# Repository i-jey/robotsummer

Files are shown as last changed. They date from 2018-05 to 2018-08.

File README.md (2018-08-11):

ENPH Second Year Summer 
=====

## Description 
Repo to host team code, docs, CAD models, circuit schematics and other useful items. 

## COMPETITION RUNS 
[Video of all teams at competition here.](https://www.youtube.com/watch?v=OxAf1p7clqE)

Our runs found at: 

* [8:40](https://youtu.be/OxAf1p7clqE?t=8m40s)

* [46:23](https://youtu.be/OxAf1p7clqE?t=46m23s)

* [1:07:25](https://youtu.be/OxAf1p7clqE?t=1h7m25s)

* [Tape follower: 57:10](https://youtu.be/OxAf1p7clqE?t=57m10s)

## Documentation site 
https://i-jey.github.io/robotsummer/

## Calculation Spreadsheet
https://docs.google.com/spreadsheets/d/1G_nlOqhw7OiXAsn64Kg7ZWVn5ETo55PLTQZf5VaNq4Y/edit#gid=240156634

## First Design Review 
https://docs.google.com/presentation/d/1Tin1bqWngJIaByWks2kfljkIxHQzdjXB50zxXt77TIM/edit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

STM32
===

## Key pins
---
|Key Pins 	|Description 	|Notes 	|
|:-:	|:-:	|:-:	|
|A9 	|TX1 	|Connect to RX on the Serial port connector 	|
|A10 	|RX1 	|Connect to TX on the Serial port connector 	|
|B6 	|SCL1 	|OLED display 	|
|B7 	|SDA1 	|OLED display 	|

## Uploading code 
---
If the code fails to upload, the error is usually one of the following: 
1. The platformio.ini is missing the `upload_protocol = serial` and `upload_port = COMX` settings.
2. RX / TX pins have been mixed up from the STM to the serial port connector. They should go to the opposite pins on the serial port connector. 
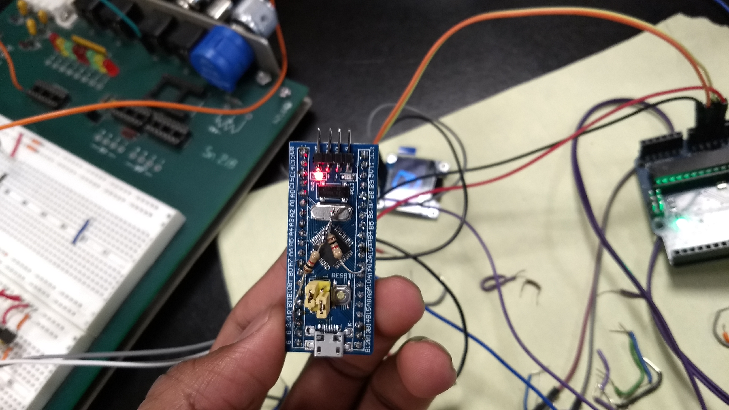
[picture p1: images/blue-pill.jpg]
3. The jumper is not in the correct position. 

## Pinout Reference
---
Pinout

Electrical Circuits
===

## High-side driver H-Bridge
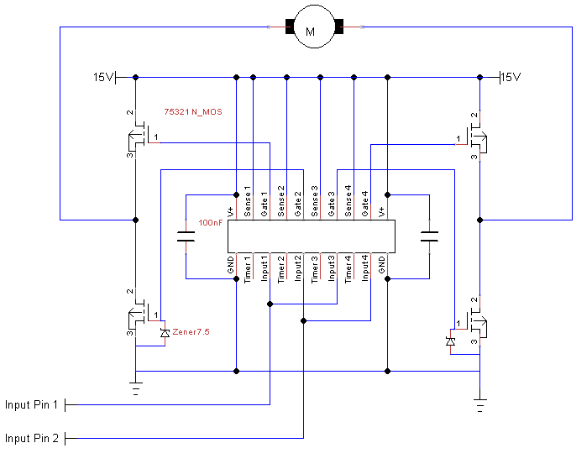
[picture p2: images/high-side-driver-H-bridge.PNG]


Wiring Check
===
1. Left Panel
2. Right Panel
3. Main Ground
4. 16V Rail
5. Control Panel Signal
6. Conntrol Panel Power
7. Potentiometer 
(FINISHED EDITING)

Tricks
===
1. Capacitors between power and ground prevent the bluepill from turning off when the H-bridges turn on. A 470uF capacitor keeps the bluepill powered at 3.3V for long enough when the voltage of the rest of the battery drops due to the sudden current draw of the h-bridges.

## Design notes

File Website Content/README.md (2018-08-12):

Documentation Materials 
=== 

Place your content in the relevant folders (images, text+explanations, diagrams). Also add any photos you have of the robot or just general lab stuff into their respective folders too.

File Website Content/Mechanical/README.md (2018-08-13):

Mechanical Components, STLs, design decisions etc.
=== 

## Chassis

PL2 W7K's chassis was constructed primarily out of lasercut hardboard. The chassis was designed in a modular fashion, separating the robot into sections containing the main functional zone, the electrical compartment, and an external drivetrain mounted underneath

## Drivetrain

PL2 W7K consisted of an external/removable drivetrain subassembly, consisting of two independent barbercoleman DC motors and a 1:3 motor-to-wheel gear ratio to provide a strong balance between torque and speed

## Claws

Mirrored side claws were implemented to enable rapid deployment and simple functionality. Constructed from waterjet sheetmetal, the outstretched arms allowed PL2 to grab and rescue ewoks without ever stopping

## Bridge deployment

Gaps in the course were tackled with a forklift-style bridge deployment mechanism. Front arms were lasercut from acrylic plastic to allow fast and controlled bridge laying

## Basket mechanism

A removable basket was also lasercut from hardboard. A metal hook was added with bearings to ensure the basket could easily slide down the zipline on the course. The basket was deployed using a platform and pulley system, powered by a continuous servo

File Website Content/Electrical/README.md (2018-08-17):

Electrical Components, Debugging, Diagrams etc.
=== 

## Motor Drivers

PL2 used H-bridges to allow motors to be driven at high voltages and currents while being controlled through low-voltage signals from the Bluepill mirco-controller. Our h-bridges consist of electrical switches (N-Type MOSFETS) controlled by a high-side gate driver IC chip which recieved PWM outputs from the Bluepill. Each H-bridge was decoupled through capacitors along input and output voltage lines so that noise propagation would not influence other componants in the electrical system.

## IR detection circuits

One of the obstacles of the course was decoding an infra-red signal beacon. This beacon was placed just before the archway, and it's signal would switch randomly between flashing at a frequency of 1kHz and 10kHz. If the robot passed throught the archway when the signal was at 1kHz a platform beyond the archway would start rotating, breaking the tape the robot used to navigate the course. PL2 had two IR detection circuits were used to differentiate the beacons 1kHz and 10kHz respectivly. Both circuits where identical, with the exception of the filter explained below.

This analog circuit was a series of signal manipulators to decode the flashing of the beacon into a signal understood by the Bluepill mirco-controller. The componants of the circuit are as followed:

1. DC-Block

      The DC-Block was used to eliminated the steady 60Hz infra-red emitted from the standard household lights as a part of the competition enviroment.
      
2. Amplify

      At a distance that was relevant to robot manuverability the signal would come across quite weak (in the milli-volts range) the amplificating was used to strengthen the incoming signal.
      
3. Active Filtering

      Since PL2 was required to differentiate 1kHz and 10kHz, the respective circuits were built using Op-Amps (Operational Amplifiers) and RC circuits to ignore the opposite frequency.

4. Analog to Digital Conversion and Amplification

      The final conversion is required to turn the detection of the appropriate signal into a digital high that the mirco-controller may interpret. An extra amplification circuit was required in the event that the non-fluctuating voltage is not large enough for the mirco-controller to read a digital high.
      
### Inverter

As a part of the analog circuits, a switching-inverter was used to supply -VCC to the operational amplifiers.

## Attempted: Encoders

Orginially it was planned to include encoders in the development of PL2 to aid in the navigation of the course. In retrospect we should have started the development of the Encoder interpretation much sooner to ensure reliable usage. The primary difficulty was recieving a steady, noise-free pulse signal from the encoders. As an encoder rotates two switches are turned on and off. The mirco-controller may interpret distance through the number of times the switches are turned on, and direction through the high/low phase shift between the two switches. Due to mechanical inaccuracies the signal was very noisy and, initially, the mirco-controller would read high when it should not have, thus, misinterpreting the signal. 

To fix this we built a RC filter circuit and Schmitt-trigger to filter out high frequency noise, and to employ hysteresis to ensure a clean pulse signal could be read by the mirco-controller. As mentioned before, this development occured too late, for we had already started to used hardcoded motor-on times for precise movements. 

## Attempted: IR Signal Direct Read

Due to the extremely fast clock cycle of the Bluepill mirco-controller (72MHz) it is very possible to directly interpret signals at a frequency in the kHz range as required for the competition. The circuit was simply an amplifier and comparator to ensure the signal was properly read, and the sine wave was converted into a pulse. This development also occurred too late in the 6 week timeline and while it did work, it was a back-up plan in the event the analog circuits failed for some unknown reason.

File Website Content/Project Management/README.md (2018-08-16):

PM Stuff, Team Collaboration etc. 
=== 

## Titles
Team #0

Robot: PL2 W7K (Pronounced "Please Work")

## The Challenge: Ewok Rescue
The 2018 ENPH253 challenge revolved around rescuing 4 plush ewoks and Chewbacca from the imperial fortress. Obstacles included two gaps/valleys in the course, an infrared-triggered spinning platform, two (optional) ziplines, and a pathless bridge separating Chewbacca from the rest of the course.

*The full rules of the competition can be found [here](https://docs.google.com/document/d/18rYIVlMZeD559deR7-5YjfQzZz4BeeS6pr8FI5Qlm8Q/edit)*

## The Strategy: Strategy and PL2 W7K
Our approach to completing the course was to have a separate mechanism for each obstacle. We designed a forklift-style mechanism to lay a bridge over the gaps. The infrared-triggered spinning platform was avoided using an active-filtering IR detection circuit. The bridge mechanism allowed us to avoid requiring the first zipline, while the second was used to transport our ewok-filled basket back to the "safe zone". The pathless bridge would be traversed using edge detection-and-follow algorithm.

PL2 was designed to be **compact**, **fast**, and **nimble**. Ewok-grabbing claws were implented in a way that allowed the robot to grab the ewoks without ever having to stop moving. Ultimatly, this was critical in our success. Since our robot could complete the course so quickly in the alotted 2 minutes we could run twice, the only robot to do so, negating any preformace deficiencies due to random unpredicable errors

## The Result: How we did
PL2 was able to consistently rescue 3 of the 5 plushies, obtaining a total of 9 points (out of 17 - Chewbacca was worth extra). Due to time constraints, we were not able to implement the second half of the course, meaning that we did not get to Chewbacca. Rather, we focused on speed and consistency, bearing us 5th place of 16 in the final competition.

## The Takeaway: What we learned
The team picked up many "dos and don'ts" along the way, as we strongly noticed what worked and what did not work. Perhaps our biggest takeaway was to plan "the small things" thoroughly to avoid spending time on them later. Examples:

- Avoid using header pins - they do not make reliable connections in wired applications

- Just commit to wire placement - Many times we were using connections that would disconnect consitantly, creating a very unreliable system. Having never designed wire managment before we were worried about changing are minds with how we did something, thus having to restart. We ended up changing how we managed our wired three times (complete reboot with solder) anyway and it would have saved time if we just commited and tried sooner.

- Decoupling Capacitors - Saved our lives. At one point when the 14.5V rail was activated and our motors started the Bluepill mirco-contoller would reset. This was likely caused through an extremly fast voltage drop along the 3.3V rail powering the mirco-contoller. A 500uF capacitor fixed that up instantly through maitining the 3.3V rail high enough for the brief moment it dropped.

- Design modularly - ensure that each part/system can be easily accessed, replaced and maintained without interfering with other systems. We learned this specifically with our powertrain. It was detachable, thus, changes could be made without invading on the rest of the chassis design.

- Continuously test - test subsystems, systems and sequences not only for functionality but also for consistency alongside development to save time debugging

- Sample size - consider outliers in your analysis but do not base your judgement single occurrences (for both failures and successes)

- Task Delegation - At some points, mainly during testing, it was not necessary for every group memeber to be present. In the event of too many people working on one componant the multitude of opinions bogged down progress. This being said, it was critical in many situations that more than one person was reviewing work to ensure mistakes where not being missed for a long time.

- Late Nights - Sometimes staying up to un-Godly hours was more of a way to have fun the work efficiently..

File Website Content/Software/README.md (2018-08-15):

Code structure, decisions, weird STM32 stuff etc.
=== 

The brain of PL2 W7K was the STM32 "Blue Pill" microcontroller. The small size, fast clock speeds, and large pinout arrays made the blue pill the top choice for a compact robot. A C++ framework enabled object-oriented Arduino-style code, allowing for modular and easily-integratable components and sequences.

## Menu/control system

A multi-menu control panel was implemented on to the side of PL2 to allow for on-the-spot value adjustment and testing.

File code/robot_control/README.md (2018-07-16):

Control Code 
=== 

VSCode and PlatformIO
--- 
1. [Download VSCode](https://code.visualstudio.com/download)
2. [Install PlatformIO](https://platformio.org/get-started/ide?install=vscode)

src/
--- 
This is where the main jazz is located. Things have been modularized so far by sequences (i.e bridge deployment sequences, claw sequence, basket sequence). You'll find `.h` and `.cpp` files here (abstracts and implementation respectively). 

All those files may have you feelin' a ways, but have no fear. The header files, `.h` are just templates that declare what functions/variables are in use for a given file (class). Reading through the header files is probably a good way to get an idea of how the code is laid out (i.e the function abstracts). `includes.h` bundles everything together so that we can reference them from the main control loop.

`main.cpp` is where the control loop runs, and where constants are set. The different sequences are called in the loop and the actual reading of sensors/writing to motors occurs within the implementation of each sequence (e.g look at `clawSequence.cpp` and `claw.cpp`). 

I need to hit up Amar to find out if it's better practice to set constants in a separate header file or what, but for now it's a minor point. 

Module overview and associated constants
--- 
* Motor 
    1. P, I, D constants
    2. PID speed
    3. PID QRD Threshold
    4. 
* Claw 
    1. a
* Bridge 
    1. b
* Basket
    1. c
* Infrared sensor
    1. d

TODO
---
`July 15th, 2018`
1. Finish adding menu options (dynamically add case values as opposed to hardcoding) 
2. Implement EEPROM to store menu values

OLD
1. <del> [Penned for later, or never lol]Create (i.e update) the current `control flow diagram`. Understand states of different sequences, when they have to override/interact with one another (e.g when ir detected we need to change claw control state, or when second bridge deploys we need to change motor control state)
2. <del>Add in a `flag` in `bridge.cpp/bridge.h` so we know when to `switch from tape following to edge detection`. After the second edge is detected we need to do some custom movement.
    - Rotate 90 left, drop bridge, move a set distance w/ wheel encoders, rotate 90 left, drive forward w/ edge detection.
3. <del>Write `Gate (IR) sequence` (i.e set flag to keep left claw raised, raise both claws going through gate). **Note**: This means `clawSequence` will probably need to be updated to chillax while the gateSequence is going on. 
4. <del>Need to think about how motor control is going to get passed around, i.e from tape control to edge detection to bridge deployment to resuming. And the again, when second edge is detected, rotation, bride deployed, edge detection initiated. (control flow diagram will help with this)
5. <del>Figure out how to set up the `menu system` (how to navigate, how to set variables) using the OLED and then start up the contorl loop. Lower priority for now, setting up base of architecture first. 
6. <del>[Changing to uint8_t breaks stuff, can figure this out later]Convert types to standard definition (i.e 8-bit unsigned integer -> uint8_t)

Lastly, thank you for reading. 

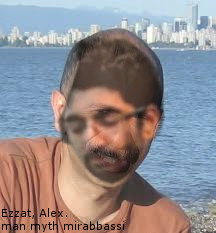
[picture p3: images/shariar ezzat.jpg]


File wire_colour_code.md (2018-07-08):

<span style="color:black">Black-Ground</span>
<br>
<span style="color:red">Red-High Voltage (15V)</span>
<br>
<span style="color:orange">Orange-Mid Voltage (5V)</span>
<br>
<span style="color:yellow">Yellow-Low Voltage (3.3V)</span>
<br>
<span style="color:purple">Purple-Intermediary Wires (High Voltage)</span>
<br>
<span style="color:blue">Blue-Intermediary Wires (Low Voltage)</span>
<br>
<span style="color:green">Green-Servo Signal</span>
<br>
<span style="color:white">White-Motor Signal</span>
<br>
<span style="color:grey">Grey-QRD Signal</span>
<br>
<span style="color:grey">Grey-IR Signal</span>

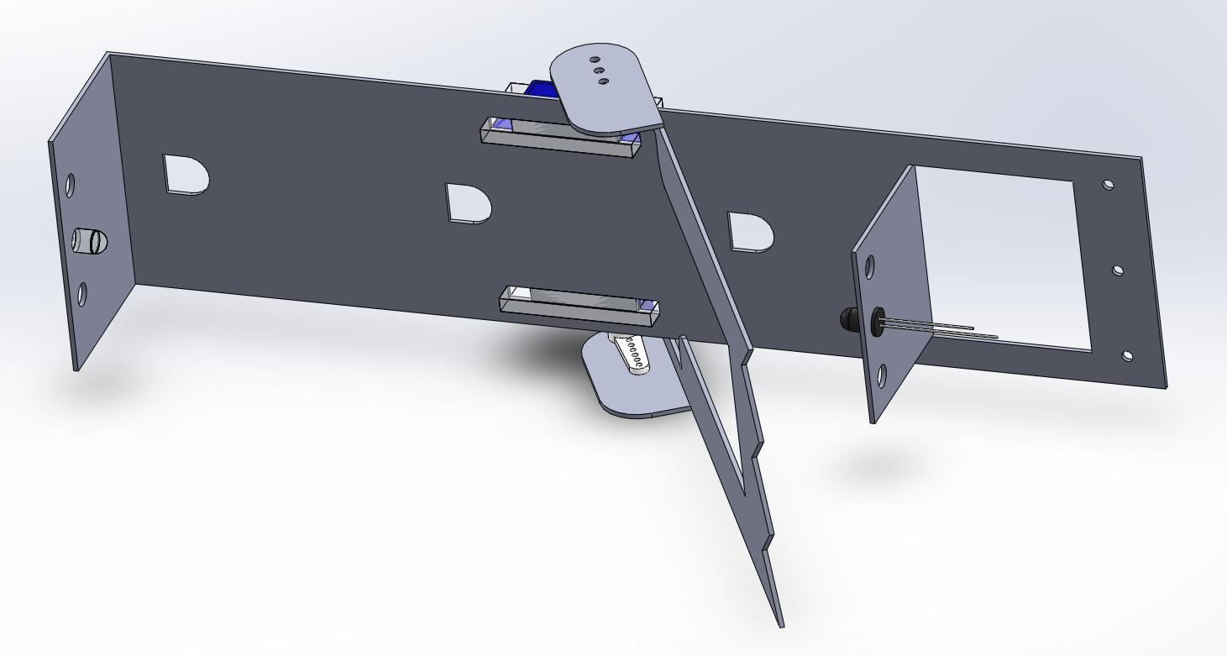
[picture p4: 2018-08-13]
Website Content/Mechanical/CADScreenshots/IsolatedArmView.PNG

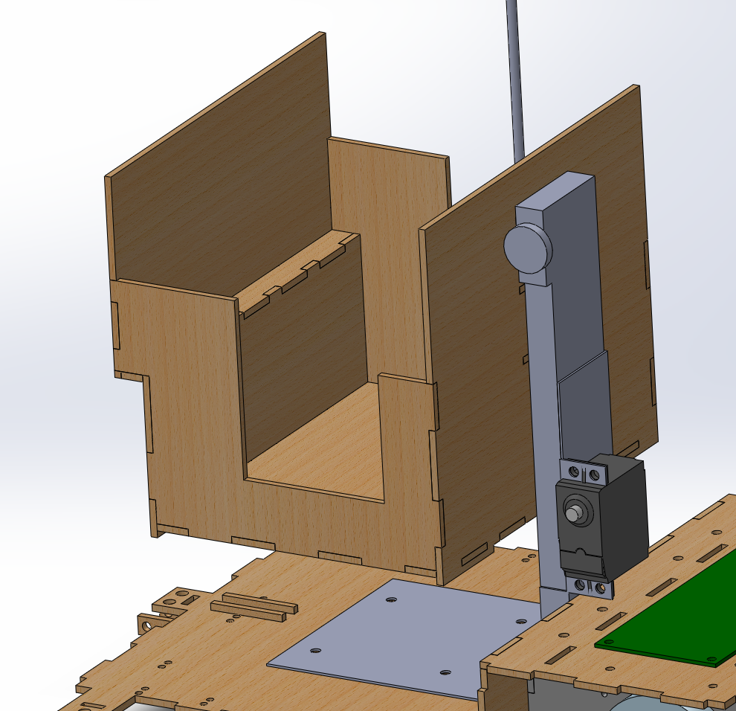
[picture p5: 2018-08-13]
Website Content/Mechanical/CADScreenshots/BasketRaisingMechanism.PNG

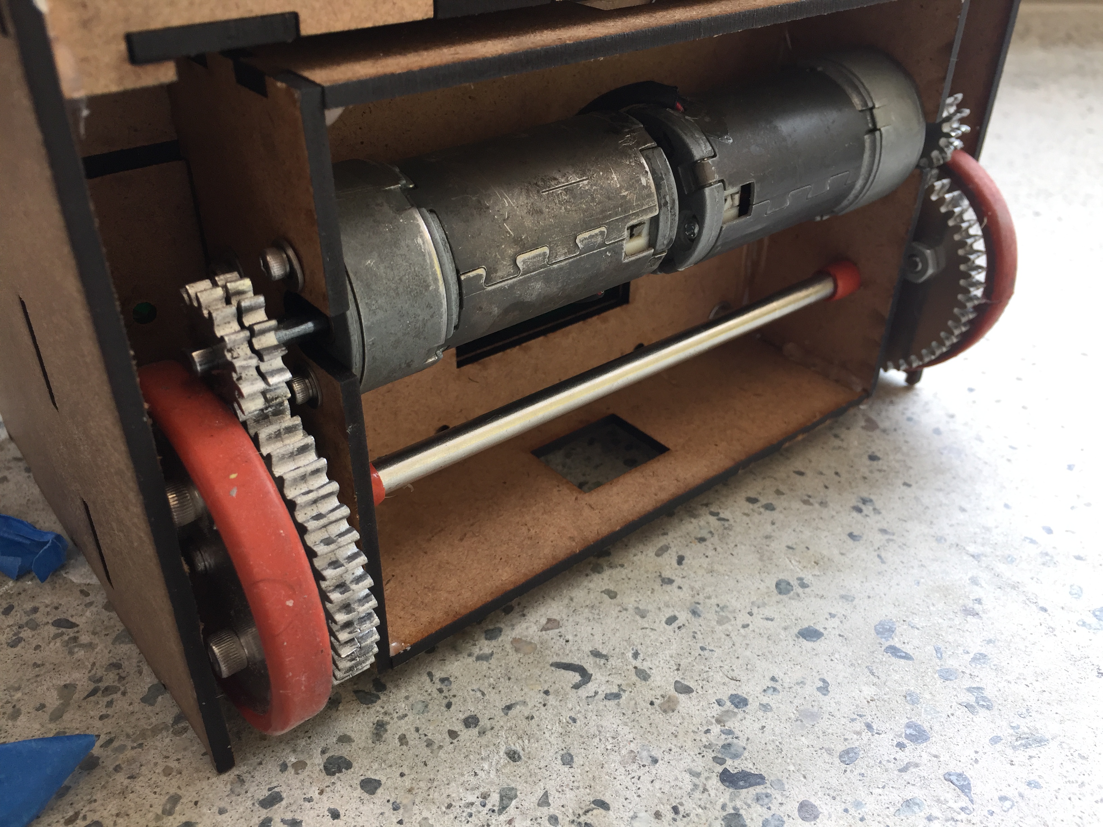
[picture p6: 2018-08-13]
Website Content/Mechanical/Drivetrain2.JPG

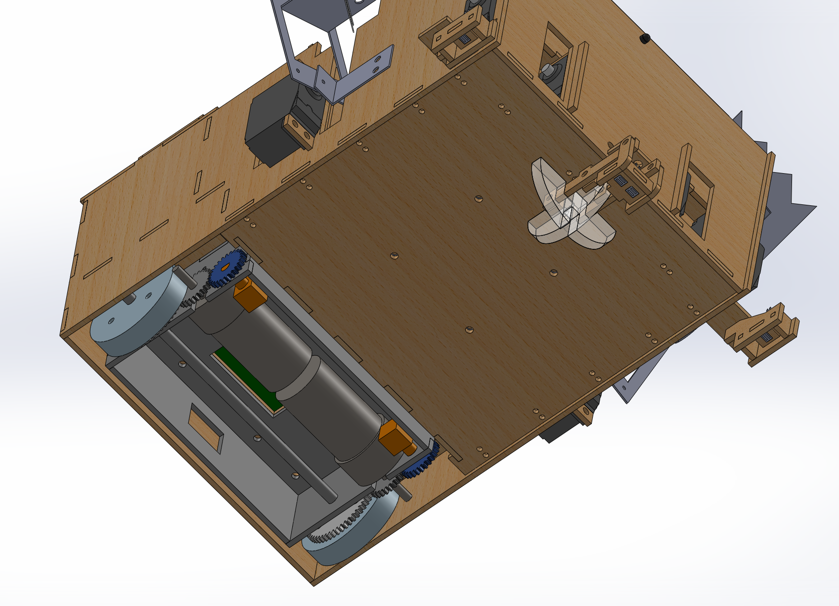
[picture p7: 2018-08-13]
Website Content/Mechanical/CADScreenshots/Drivetrain&BottomView.PNG

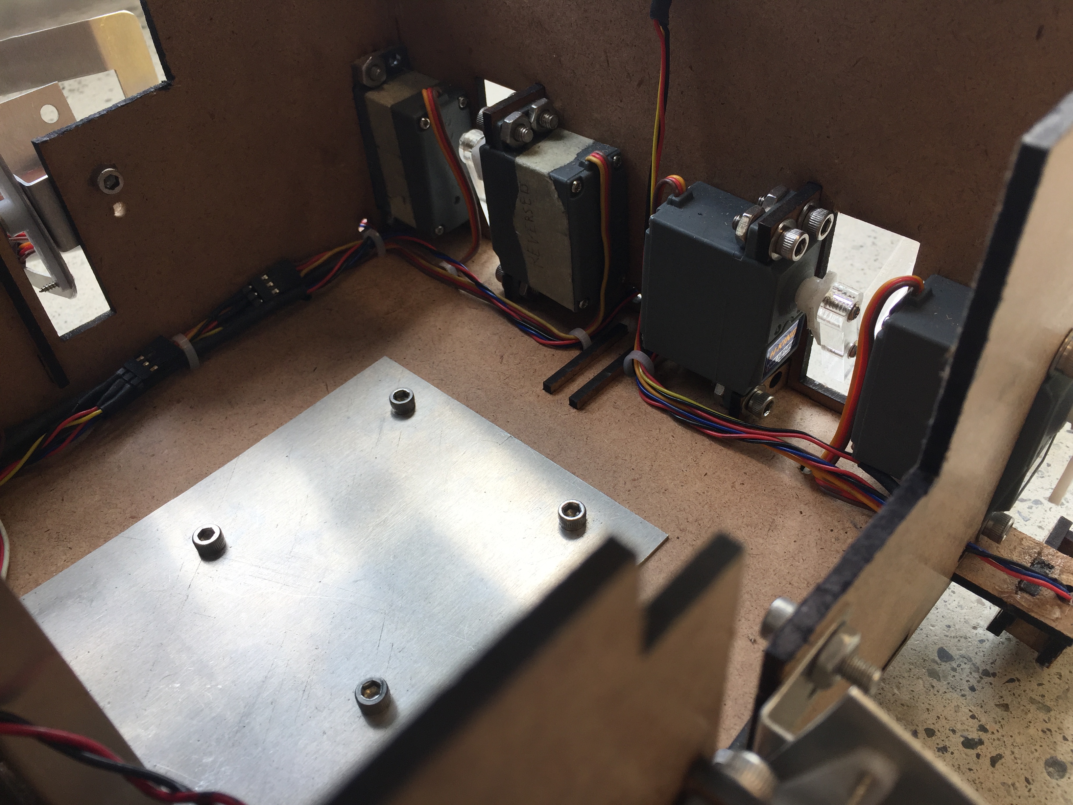
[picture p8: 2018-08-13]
Website Content/photos_of_robot/InsideChassis3.JPG

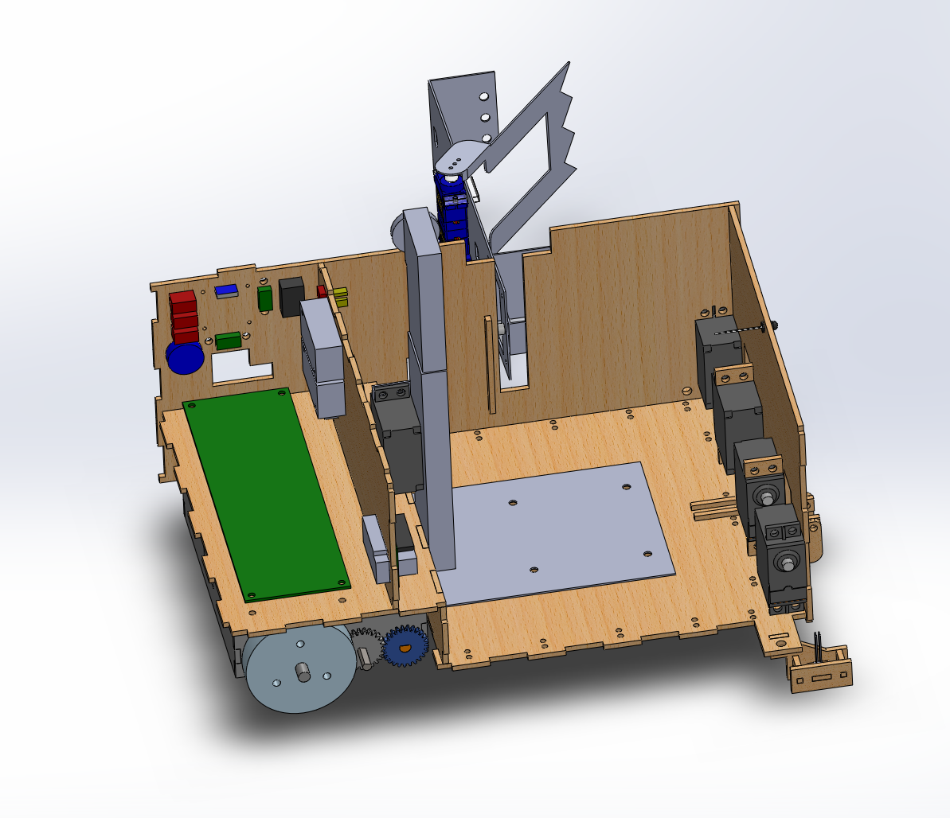
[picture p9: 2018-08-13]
Website Content/Mechanical/CADScreenshots/OpenView.PNG

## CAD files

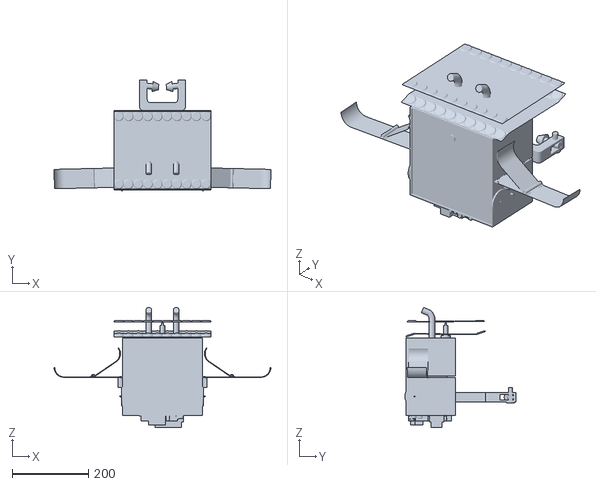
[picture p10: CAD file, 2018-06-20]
cad_models/LukeSkyWaltham.STL
568.9 x 292.2 x 315.1

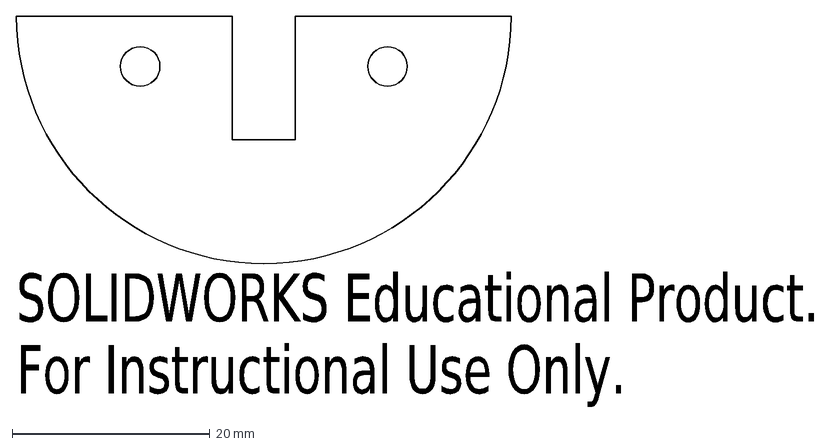
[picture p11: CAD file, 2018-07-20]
cad_models/V3/Acrylic parts/SliderPc1.DXF
SOLIDWORKS Educational Product.
For Instructional Use Only.

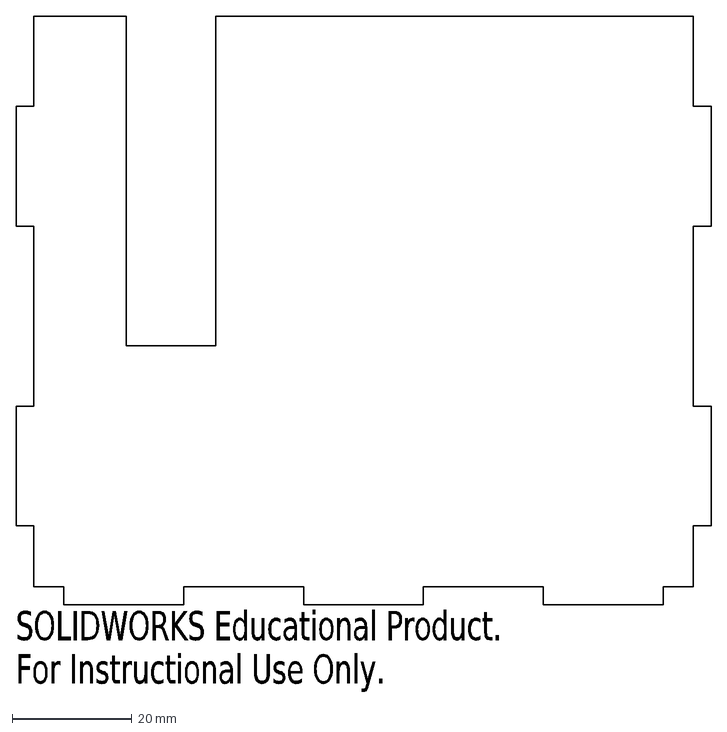
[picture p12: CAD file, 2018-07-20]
cad_models/V3/Basket/BasketV3SidePanelx2.DXF
SOLIDWORKS Educational Product.
For Instructional Use Only.

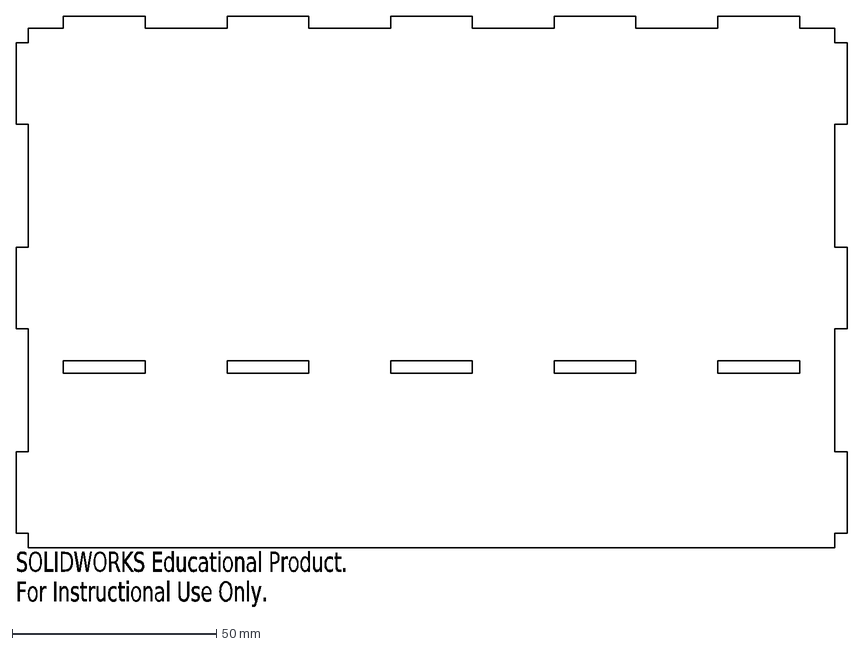
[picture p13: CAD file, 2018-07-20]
cad_models/V3/Chassis/ChassisV3BackPanel.DXF
SOLIDWORKS Educational Product.
For Instructional Use Only.

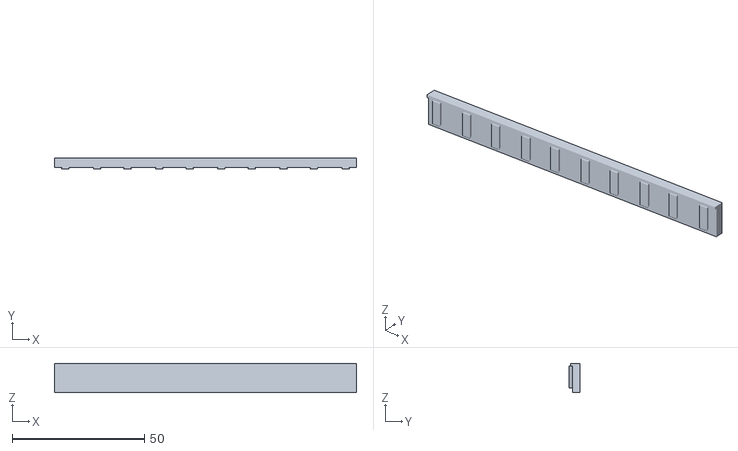
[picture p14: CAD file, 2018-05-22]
docs/AlexEzzat_54_MaleSide.STL
114.2 x 4.30 x 11.0

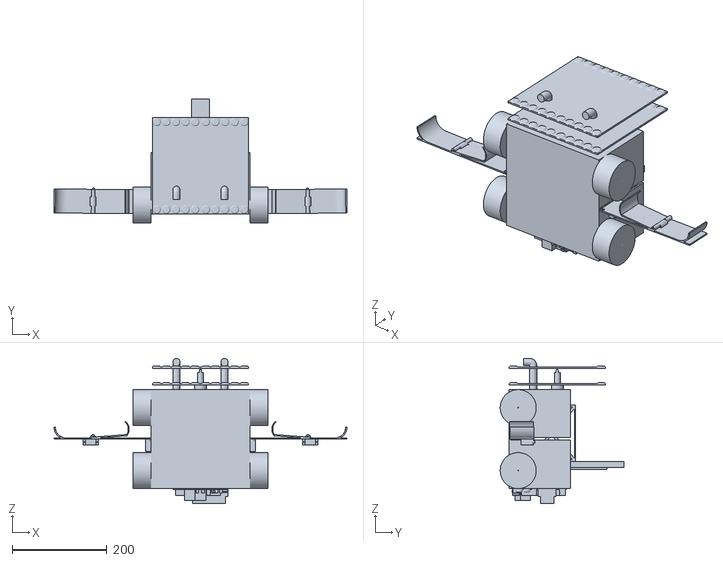
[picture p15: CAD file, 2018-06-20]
cad_models/DoubleBridger.STL
619.4 x 261.3 x 306.9

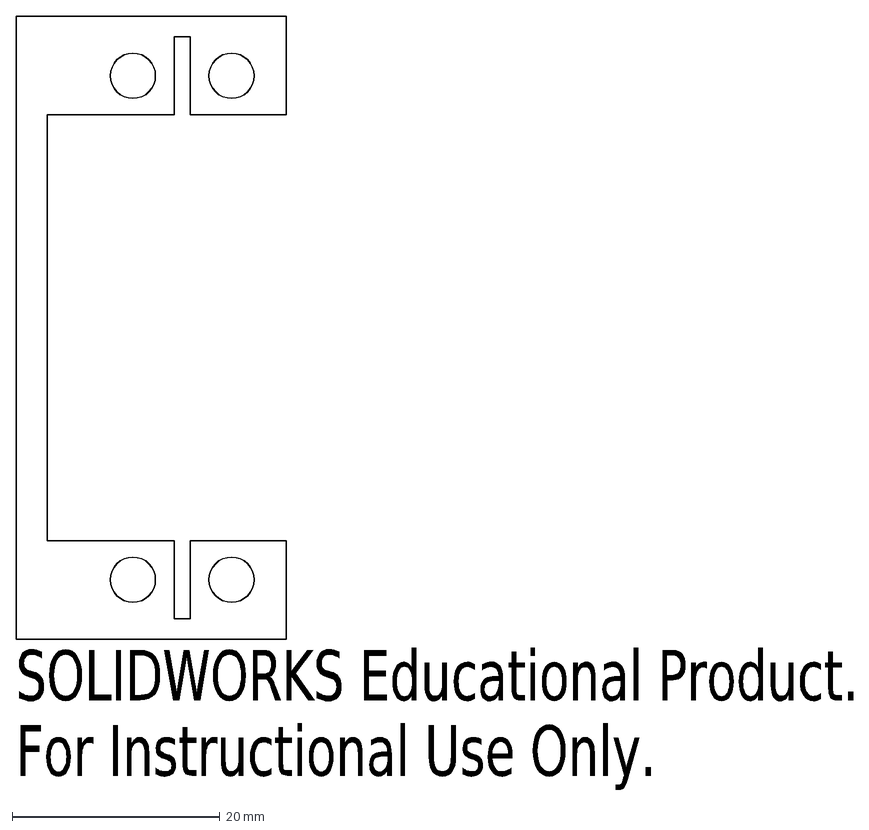
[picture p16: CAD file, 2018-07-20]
cad_models/V3/Acrylic parts/LargeServoHolderx4.DXF
SOLIDWORKS Educational Product.
For Instructional Use Only.

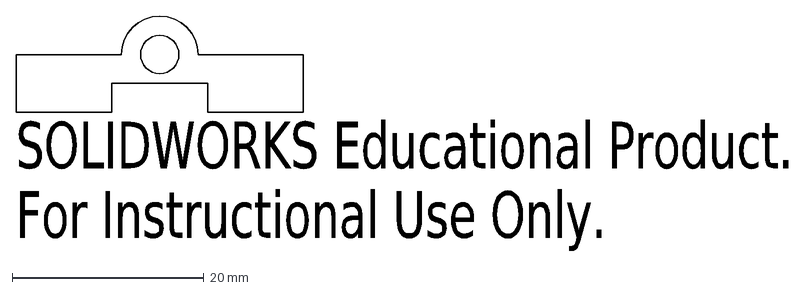
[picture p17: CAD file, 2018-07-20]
cad_models/V3/Basket/BasketRodHolderx3.DXF
SOLIDWORKS Educational Product.
For Instructional Use Only.

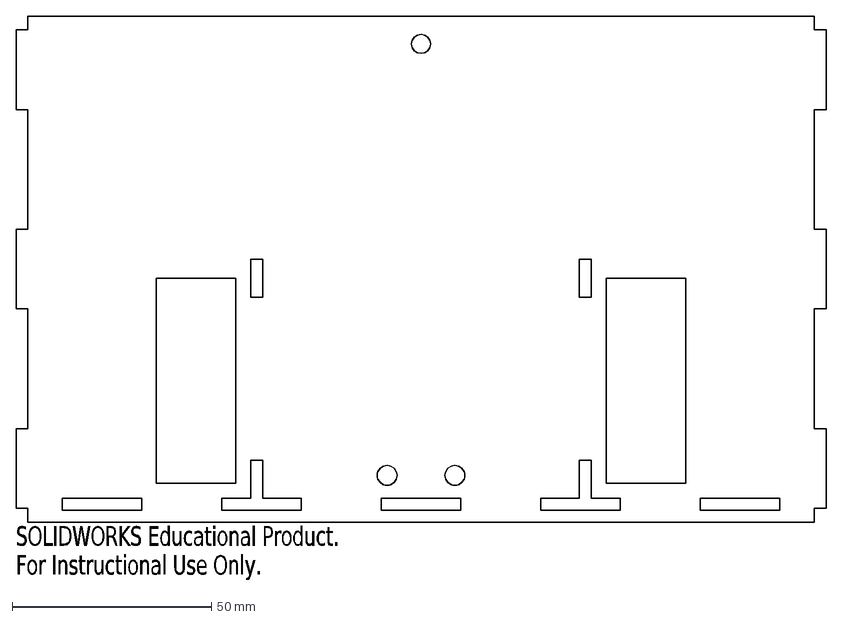
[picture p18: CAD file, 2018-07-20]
cad_models/V3/Chassis/ChassisV3FrontPanel.DXF
SOLIDWORKS Educational Product.
For Instructional Use Only.

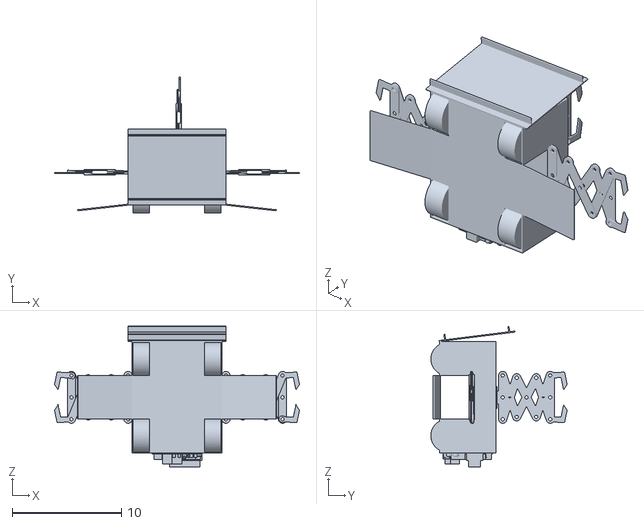
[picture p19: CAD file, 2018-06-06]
cad_models/FlatBot.STL
22.4 x 12.5 x 12.8

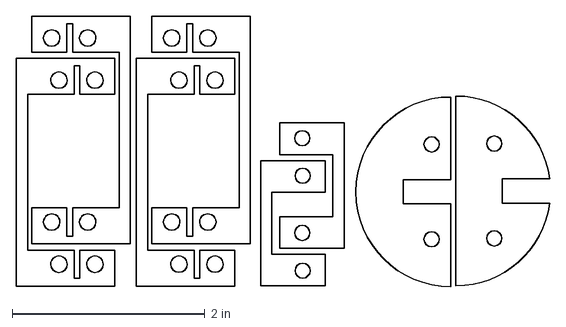
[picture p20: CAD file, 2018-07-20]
cad_models/V3/Acrylic parts/Acrylic DXF.dxf
5.54 x 2.81 in

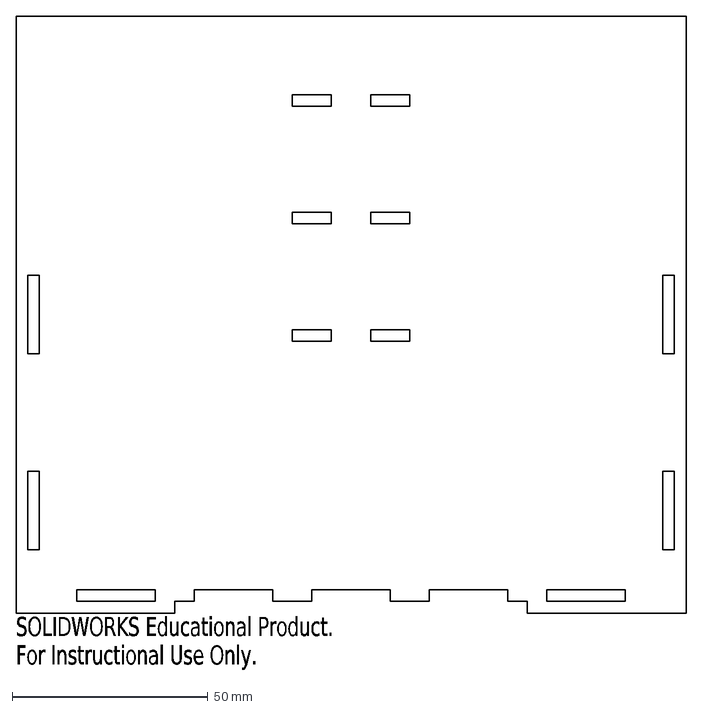
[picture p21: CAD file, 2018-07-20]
cad_models/V3/Basket/BasketV3BackPanel.DXF
SOLIDWORKS Educational Product.
For Instructional Use Only.

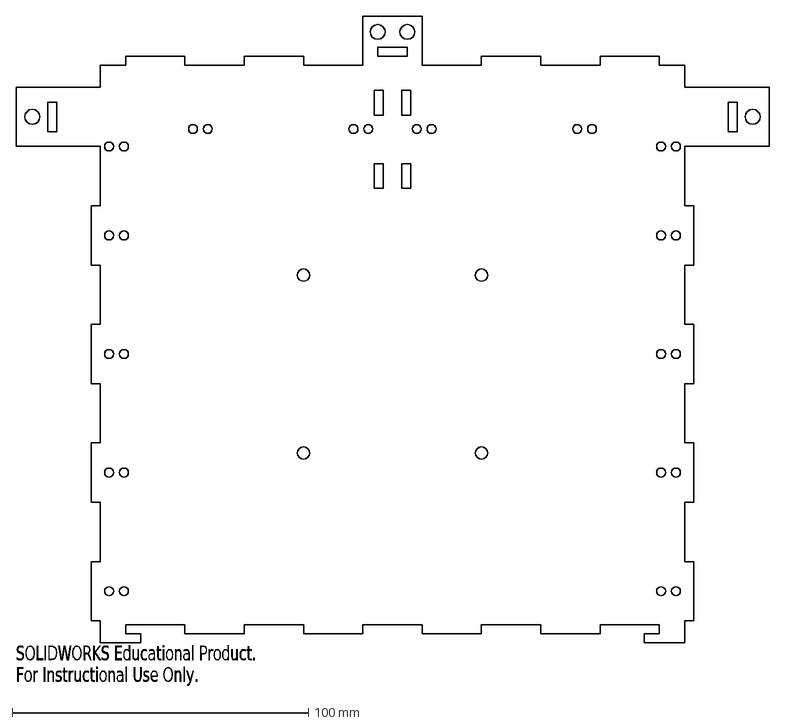
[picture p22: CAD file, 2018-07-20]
cad_models/V3/Chassis/ChassisV3LowerBottomPanel.DXF
SOLIDWORKS Educational Product.
For Instructional Use Only.

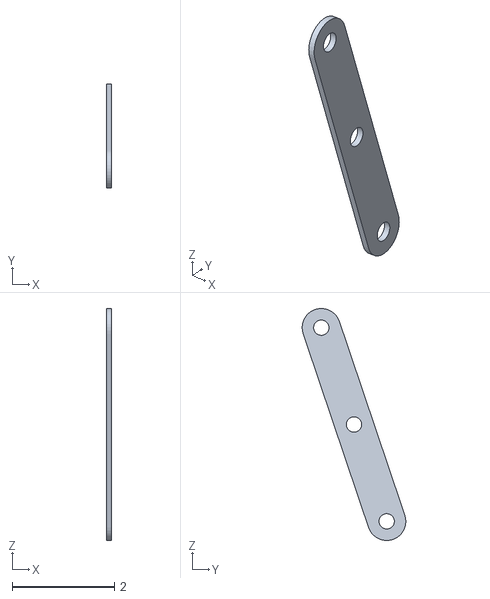
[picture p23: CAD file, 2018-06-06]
cad_models/FlatBot - Claw Arm-3 Claw Arm BracketComponent-2.STL
0.1 x 2.03 x 4.54

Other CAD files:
cad_models/V3/Acrylic parts/SliderPc2.DXF
cad_models/V3/Basket/BasketV3FrontPanel.DXF
cad_models/V3/Chassis/BatteryHolderSidePanelx2.DXF
cad_models/FlatBot - TINAH board-1.STL
cad_models/FlatBot - 3in Wheel-1.STL
cad_models/FlatBot - 3in Wheel-2.STL
cad_models/FlatBot - 3in Wheel-3.STL
cad_models/FlatBot - 3in Wheel-4.STL
cad_models/FlatBot - Bridge-1.STL
cad_models/FlatBot - Chassis Lid-1.STL
cad_models/FlatBot - Chassis Ramp-1.STL
cad_models/FlatBot - Chassis Ramp-2.STL
cad_models/FlatBot - Claw Arm-1 Claw Arm BracketComponent-1.STL
cad_models/FlatBot - Claw Arm-1 Claw Arm BracketComponent-2.STL
cad_models/FlatBot - Claw Arm-1 Claw Arm BracketComponent-3.STL
cad_models/FlatBot - Claw Arm-1 Claw Arm BracketComponent-4.STL
cad_models/FlatBot - Claw Arm-1 Claw Arm BracketComponent-5.STL
cad_models/FlatBot - Claw Arm-1 Claw Arm BracketComponent-6.STL
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

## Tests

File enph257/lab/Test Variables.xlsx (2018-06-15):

 | Variables
Test Number | c | k | Pin | kc | e
1 | 921 | 300 | 10 | 12.5 | 0.2
2 | 921 | 500 | 11 | 12.5 | 0.2
3 | 1400 | 200 | 11 | 15 | 0.4
Changed Starting Tempurature
4 | 1200 | 200 | 8.5 | 9.25 | 0.4
5 | 1400 | 200 | 8.5 | 9.25 | 0.4
6 | 1200 | 175 | 12.5 | 9.5 | 0.2
7 | 1300 | 175 | 10 | 8 | 0.25
7 | 1100 | 250 | 10 | 8 | 0.25
9 | 1100 | 150 | 11 | 8 | 0.2
10 | 921 | 220 | 11.5 | 8.2 | 0.2

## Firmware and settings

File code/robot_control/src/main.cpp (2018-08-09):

#include "includes.h"
#pragma GCC diagnostic ignored "-Wwrite-strings"

constexpr int INSIDE = 1; 

// Global variable initialization 
int globalMotorStateTracker = 0; 
int prevEwokCounter = 0; 
int ewokCounter = 0; 
int rightClawState = 0; 
int leftClawState = 0; 

// EEPROM / menu reference 
enum MenuItems {
    menu_qrdThreshold,
    menu_p,
    menu_d, 
    menu_gain,  
    menu_defaultSpeed, 
    edgeThresh, 
    firstBridgeLowerAngle, 
    firstBridgeUpperAngle, 
    edgeReverseDistance, 
    dropBridgeDistance, 
    driveOverDistance, 
    s3Tilt, 
    s3Reverse, 
    s3Drop, 
    s3Pullback, 
    pidTime, 
};

// Menu pins 
constexpr int startBtn = PC15;
constexpr int menuMinus = PA12; 
constexpr int menuToggle = PA15; 
constexpr int menuPlus = PA11; 
constexpr int menuPot = PB1; 

// Oled pins 
constexpr int oled_scl = PB10; 
constexpr int oled_sda = PB11; 
OLED oled(oled_scl, oled_sda, 8); 
extern uint8_t SmallFont[];

// Motor pins 
constexpr int right_motor_pin1 = PA0; 
constexpr int right_motor_pin2 = PA1; 
constexpr int left_motor_pin1 = PA2; 
constexpr int left_motor_pin2 = PA3; 

// Encoder 
constexpr int encoderLeft = PB14; 
constexpr int encoderRight = PB15; 

// PID QRDs 
constexpr int right_pid_QRD = PA4; 
constexpr int left_pid_QRD = PA6; 

// Edge QRDs 
constexpr int right_edge_QRD = PA5; 
constexpr int left_edge_QRD = PA7; 

// Bridge pins 
constexpr int bridgePin1 = PB9; 
constexpr int bridgePin2 = PA10; 

// Right claw pins 
constexpr int right_clamp_pin = PB8; 
constexpr int right_arm_pin = PB7; 
constexpr int right_trigger = PB4; 

// Left claw pins 
constexpr int left_clamp_pin = PB6;
constexpr int left_arm_pin = PB0; 
constexpr int left_trigger = PB3; 

// IR Pins 
constexpr int irPin1k = PB13;
constexpr int irPin10k = PB12;  

// Basket pin 
constexpr int basketServo = PA8; 
constexpr int basketLim = PC13; 

// Bridge 
int edgeThreshold = 500; 
int bridge1LowerAngle = 40; 
int bridge1UpperAngle = 115; 
int bridge2LowerAngle = 60; 
int bridge2UpperAngle = 165; 

// PID constants
int p = 0;
int i = 0; 
int d = 0;
int gain = 0;
int qrdThreshold = 0; 
int defaultSpeed = 120; 

// Claw 
int leftClawCloseAngle = 177; 
int leftClawOpenAngle = 60; 
int leftClawOpenAngleInside = 70; 
int leftClawLowerAngle = 20; 
int leftClawRaiseAngle = 180; 
int leftVertical = 153; 
int leftPhoenix = 68; 
int leftDab = 81; 

int rightClawCloseAngle = 0; 
int rightClawOpenAngle = 105; 
int rightClawOpenAngleInside = 78; 
int rightClawLowerAngle = 160; 
int rightClawRaiseAngle = 20; 
int rightVertical = 60; 
int rightPhoenix = 81; 
int rightDab = 18; 

int closeTime = 250; 
int raiseTime = 1000; 
int openTime = 500; 
int closeTime2 = 500; 
int lowerTime = 1000; 
int resetTime = 1000; 

// Menu bools 
bool start; 
bool toggle = false; 

// Construct modules 
Basket basket = Basket(basketServo, basketLim); 
Bridge bridge = Bridge(bridgePin1, bridgePin2, left_edge_QRD, right_edge_QRD, edgeThreshold, bridge1LowerAngle, bridge1UpperAngle, bridge2LowerAngle, bridge2UpperAngle); 
Arm leftArm = Arm(left_clamp_pin, left_arm_pin, left_trigger, leftClawCloseAngle, leftClawOpenAngle, leftClawOpenAngleInside, leftClawLowerAngle, leftClawRaiseAngle, leftVertical, leftPhoenix); 
Arm rightArm = Arm(right_clamp_pin, right_arm_pin, right_trigger, rightClawCloseAngle, rightClawOpenAngle, rightClawOpenAngleInside, rightClawLowerAngle, rightClawRaiseAngle, rightVertical, rightPhoenix); 
ClawSequence leftClaw = ClawSequence(leftArm, closeTime, raiseTime, openTime, closeTime2, lowerTime, resetTime); 
ClawSequence rightClaw = ClawSequence(rightArm, closeTime, raiseTime, openTime, closeTime2, lowerTime, resetTime); 
IRReader ir =  IRReader(irPin1k, irPin10k); 
Motor leftMotor = Motor(left_motor_pin1, left_motor_pin2); 
Motor rightMotor = Motor(right_motor_pin1, right_motor_pin2); 
TapeFollow pidControl = TapeFollow(left_pid_QRD, right_pid_QRD); 
MotorControl motorControl = MotorControl(leftMotor, rightMotor, bridge, ir, basket, pidControl, leftClaw, rightClaw, qrdThreshold, gain, p, i, d);
MotorInit motorInit = MotorInit(); 

void setup() {  
    // Serial.begin(9600);

    // Menu dials
    pinMode(startBtn, INPUT_PULLDOWN);
    pinMode(menuPlus, INPUT_PULLDOWN); 
    pinMode(menuToggle, INPUT_PULLDOWN);
    pinMode(menuMinus, INPUT_PULLDOWN); 
    pinMode(menuPot, INPUT); 
    start = digitalRead(startBtn);  

    bridge.begin(); 
    leftMotor.begin(); 
    rightMotor.begin(); 
    basket.begin(); 
    leftClaw.begin(); 
    rightClaw.begin(); 
    pidControl.begin(); 
    ir.begin(); 

    // motorControl.begin();
    oled.begin(); 
    oled.setFont(SmallFont); 
    basket.begin(); 
}

void writeToEEPROM(int loc, int val) {
    EEPROM.write(loc*2+1, val&255);
    EEPROM.write(loc*2, val>>8);  
}

int16_t readFromEEPROM(int loc) { 
    return (EEPROM.read(loc*2)<<8)|EEPROM.read(loc*2+1);
}

void initializeFromEEPROM() { 
    // Motor control values
    p = readFromEEPROM(MenuItems::menu_p); motorControl.updateP(p); 
    i = 0; motorControl.updateI(i);
    d = readFromEEPROM(MenuItems::menu_d); motorControl.updateD(d); 
    gain = readFromEEPROM(MenuItems::menu_gain); motorControl.updateGain(gain);
    qrdThreshold = readFromEEPROM(MenuItems::menu_qrdThreshold); motorControl.updateThreshold(qrdThreshold);
    defaultSpeed = readFromEEPROM(MenuItems::menu_defaultSpeed); motorControl.updateDefaultSpeed(defaultSpeed);
    motorControl.edgeReverseDistance = readFromEEPROM(MenuItems::edgeReverseDistance); 
    motorControl.dropBridgeDistance = readFromEEPROM(MenuItems::dropBridgeDistance); 
    motorControl.driveOverDistance = readFromEEPROM(MenuItems::driveOverDistance); 
    motorControl.irPidTime = readFromEEPROM(MenuItems::pidTime); 

    // Bridge values 
    edgeThreshold = readFromEEPROM(MenuItems::edgeThresh); motorControl.updateEdgeThreshold(edgeThreshold);

    // Default values after flashing 
    if (p == -1) {p = 5; motorControl.updateP(p);}
    if (d == -1) {d = 5; motorControl.updateD(d);}
    if (gain == -1) {gain = 13; motorControl.updateGain(gain);}
    if (defaultSpeed == -1) {defaultSpeed = 210; motorControl.updateDefaultSpeed(defaultSpeed);}

    if (motorControl.edgeReverseDistance == -1) {motorControl.edgeReverseDistance = 300;}
    if (motorControl.dropBridgeDistance == -1) {motorControl.dropBridgeDistance = 420;}
    if (motorControl.driveOverDistance == -1) {motorControl.driveOverDistance = 1100;}
    if (edgeThreshold == -1) {edgeThreshold = 900; motorControl.updateEdgeThreshold(edgeThreshold);}
    if (qrdThreshold == -1) {qrdThreshold = 900; motorControl.updateThreshold(qrdThreshold);}
    if (motorControl.irPidTime == -1) {motorControl.irPidTime = 800;}

    if (motorControl.s3TiltLeftTime == -1) {motorControl.s3TiltLeftTime = 650;}
    if (motorControl.s3ReverseTime == -1) {motorControl.s3ReverseTime = 250;}
    if (motorControl.s3LeftPullBackTime == -1) {motorControl.s3LeftPullBackTime = 100;}
}

int optionState = 0; 
void pidMenu() { 
    int potVal = analogRead(menuPot) / 10; 
    
    oled.print("PID Menu", 0, 0); 
    oled.print("thresh: ", 0, 10); 
    oled.print("p: ", 0, 20); 
    oled.print("d: ", 0, 30); 
    oled.print("gain: ", 0, 40); 
    oled.print("Speed: ", 0, 50); 

    delay(125); // Debouncing delay 

    if (digitalRead(menuPlus)) {
        if (optionState >= 4)  {
            optionState = 0;
        }
        else {
            optionState++;
        }
    }
    // edit-view toggle 
    if (digitalRead(menuMinus)) {toggle = !toggle;}

    oled.printNumI(pidControl.getLeftQRDReading(), 45, 10);
    oled.printNumI(pidControl.getRightQRDReading(), 75, 10); 
    oled.printNumI(qrdThreshold, RIGHT, 10);
    oled.printNumI(p, RIGHT, 20);
    oled.printNumI(d, RIGHT, 30);
    oled.printNumI(gain, RIGHT, 40); 
    oled.printNumI(defaultSpeed, RIGHT, 50); 
    oled.print("<--", 45, (optionState+1)*10); 

    if (toggle) { 
        oled.print("Edit", RIGHT, 0); 
    
        switch (optionState) { 
            case MenuItems::menu_p:
                p = potVal; 
                writeToEEPROM(MenuItems::menu_p, p); 
                motorControl.updateP(p);
                break; 
            case MenuItems::menu_d: 
                d = potVal; 
                writeToEEPROM(MenuItems::menu_d, d); 
                motorControl.updateD(d); 
                break; 
            case MenuItems::menu_gain: 
                gain = potVal; 
                writeToEEPROM(MenuItems::menu_gain, gain); 
                motorControl.updateGain(gain);
                break; 
            case MenuItems::menu_qrdThreshold: 
                qrdThreshold = 10*potVal; 
                writeToEEPROM(MenuItems::menu_qrdThreshold, qrdThreshold); 
                motorControl.updateThreshold(qrdThreshold);
                pidControl.updateThreshold(qrdThreshold); 
                break; 
            case MenuItems::menu_defaultSpeed: 
                defaultSpeed = potVal; 
                writeToEEPROM(MenuItems::menu_defaultSpeed, defaultSpeed); 
                motorControl.updateDefaultSpeed(defaultSpeed); 
                motorControl.updateSpeed(defaultSpeed); 
                break; 
            default:
                break; 
        }
    }
    else {
         oled.print("View", RIGHT, 0); 
    }
}

void bridgeMenu() { 
    int potVal = analogRead(menuPot); 

    oled.print("Bridge Menu", 0, 0); 
    oled.print("Thresh: ", 0, 10); 
    oled.print("Reverse1 time: ", 0, 20); 
    oled.print("Reverse2 time: ", 0, 30); 
    oled.print("Over time: ", 0, 40); 
    oled.print("IR Pid time: ", 0, 50); 
    oled.print("<--", 45, (optionState+1)*10); 

    delay(125); // Debouncing delay 

    if (digitalRead(menuPlus)) { 
        if (optionState >= 4) { 
            optionState = 0; 
        }
        else { 
            optionState++; 
        }
    }

    // edit-view toggle 
    if (digitalRead(menuMinus)) {toggle = !toggle;}

    // Print current values 
    oled.printNumI(edgeThreshold, RIGHT, 10); 
    oled.printNumI(bridge.getLeftEdgeReading(), 45, 10); 
    oled.printNumI(bridge.getRightEdgeReading(), 75, 10); 
    oled.printNumI(motorControl.edgeReverseDistance, RIGHT, 20); 
    oled.printNumI(motorControl.dropBridgeDistance, RIGHT, 30); 
    oled.printNumI(motorControl.driveOverDistance, RIGHT, 40); 
    oled.printNumI(motorControl.irPidTime, RIGHT, 50);

    if (toggle) { 
        oled.print("Edit", RIGHT, 0); 
    
        switch (optionState) { 
            case 0:
                edgeThreshold = (potVal / 10) * 10; 
                writeToEEPROM(MenuItems::edgeThresh, edgeThreshold); 
                motorControl.updateEdgeThreshold(edgeThreshold); 
                break; 
            case 1: 
                motorControl.edgeReverseDistance = potVal; 
                writeToEEPROM(MenuItems::edgeReverseDistance, motorControl.edgeReverseDistance); 
                break; 
            case 2: 
                motorControl.dropBridgeDistance = potVal; 
                writeToEEPROM(MenuItems::dropBridgeDistance, motorControl.dropBridgeDistance);
                break; 
            case 3: 
                motorControl.driveOverDistance = potVal; 
                writeToEEPROM(MenuItems::driveOverDistance, motorControl.driveOverDistance);                
                break;
            case 4: 
                motorControl.irPidTime = potVal; 
                writeToEEPROM(MenuItems::pidTime, motorControl.irPidTime); 
                break; 
            default:
                break; 
        }
    }
    else {
         oled.print("View", RIGHT, 0); 
    }
}

void postTrooperMenu() { 
    int potVal = analogRead(menuPot); 

    oled.print("Post Stormtrooper Menu", 0, 0); 
    oled.print("Tilt left: ", 0, 10);
    oled.print("Reverse: ", 0, 20); 
    oled.print("Drop ewok: ", 0, 30); 
    oled.print("Left pull back: ", 0, 40); 
    oled.print("<--", 45, (optionState+1)*10); 

    delay(125); // debouncing delay

    if (digitalRead(menuPlus)) { 
        if (optionState >= 3) { 
            optionState = 0; 
        }
        else { 
            optionState++; 
        }
    }

    // edit-view toggle
    if (digitalRead(menuMinus)) {toggle = !toggle;}

    // Print current values
    oled.printNumI(motorControl.s3TiltLeftTime, RIGHT, 10); 
    oled.printNumI(motorControl.s3ReverseTime, RIGHT, 20);
    oled.printNumI(motorControl.dropEwokTime, RIGHT, 30); 
    oled.printNumI(motorControl.s3LeftPullBackTime, RIGHT, 40); 


    if (toggle) { 
        oled.print("Edit", RIGHT, 0); 

        switch (optionState) { 
            case 0: 
                motorControl.s3TiltLeftTime = potVal; 
                writeToEEPROM(MenuItems::s3Tilt, motorControl.s3TiltLeftTime); 
                break; 
            case 1: 
                motorControl.s3ReverseTime = potVal; 
                writeToEEPROM(MenuItems::s3Reverse, motorControl.s3ReverseTime); 
                break; 
            case 2: 
                motorControl.dropEwokTime = potVal; 
                writeToEEPROM(MenuItems::s3Drop, motorControl.dropEwokTime); 
                break; 
            case 3: 
                motorControl.s3LeftPullBackTime = potVal; 
                writeToEEPROM(MenuItems::s3Pullback, motorControl.s3LeftPullBackTime); 
                break; 
        default: 
            break; 
        }
    }
    else { 
        oled.print("View", RIGHT, 0); 
    }
}

void competitionValueInitialization() { 
    delay(150); 
    if (digitalRead(menuToggle)) {
        toggle = !toggle; 
    }

    if (toggle) { 
        // LEFT SURFACE 

        // Set values
        motorControl.leftClawDownDelay = 3300; 
        motorControl.irPidTime = 700; 
        motorControl.updateDefaultSpeed(190); 

        // Display
        oled.print("Left surface", 0, 0); 
        oled.print("claw down time: ", 0, 10);
        oled.printNumI(motorControl.leftClawDownDelay, RIGHT, 10);  
        oled.print("ir pid time: ", 0, 20);
        oled.printNumI(motorControl.irPidTime, RIGHT, 20);  

    }
    else {
        motorControl.leftClawDownDelay = 3400; 
        motorControl.irPidTime = 700; 

        oled.print("Right surface", 0, 0); 
        oled.print("claw down time", 0, 10); 
        oled.printNumI(motorControl.leftClawDownDelay, RIGHT, 10);
        oled.print("ir pid time: ", 0, 20);
        oled.printNumI(motorControl.irPidTime, RIGHT, 20);  
    }
}
bool initialize = true; 
bool initMotors = true; 
int switchMenus = 0; 

void loop() {  
    start = digitalRead(startBtn); 
    if (!start) { 
        // Stop motors 
        leftMotor.write(0); 
        rightMotor.write(0); 

        // Both claws up 
        leftArm.close(); leftArm.verticalRaise(); 
        rightArm.close(); rightArm.verticalRaise(); 
        
        // Hold basket
        basket.holdBasket(); 

        // Raise bridges
        bridge.raiseBoth(); 

        if (initialize) {
            initializeFromEEPROM(); 
            initialize = false;
            basket.raiseBasket(); 
        }
        if (digitalRead(menuToggle)) {
            if (switchMenus == 2) {
                switchMenus = 0;
            }
            else { 
                switchMenus++;
            }
            optionState = 0;
        }
        oled.clrScr(); 
        competitionValueInitialization(); 
        // if (switchMenus == 0) { 
        //     pidMenu(); 
        // }
        // else if (switchMenus == 1) { 
        //     bridgeMenu();   
        // }
        // else if (switchMenus == 2) { 
        //     postTrooperMenu(); 
        // }

        oled.update();  
        initMotors = true; 
    }
    else {
        if (initMotors) {
            initMotors = false; 
            
            motorInit.init();

            oled.clrScr(); 
            oled.print("PL2 W0RK", 40, 50); 
            oled.update(); 
            
            // reset global values 
            prevEwokCounter = 0; 
            ewokCounter = 0; 
            motorControl.reset(); 
            bridge.raiseBoth(); 

            motorControl.stateOverride(2, 0); // state 0 = continuous forward drive
            leftArm.verticalRaise(); leftArm.close(); leftClaw.stateOverride(10); 
            // leftArm.lower(); leftArm.open(!INSIDE); leftClaw.stateOverride(0);
            rightArm.lower(); rightArm.open(!INSIDE); rightClaw.stateOverride(0); 

            oled.print("2", 60, 30); oled.update(); 
            delay(1000); 

            oled.print("1", 60, 30); oled.update(); 
            delay(1000); 
        }

        oled.clrScr();
        oled.print("PL2 W0RK", 40, 0); 
        oled.print("Current state: ", 0, 20);
        oled.printNumI(globalMotorStateTracker, RIGHT, 20);  
        oled.print("Ewok counter: ", 0, 30);
        oled.printNumI(ewokCounter, RIGHT, 30); 
        oled.printNumI(leftClaw.getState(), 50, 40); 
        oled.printNumI(rightClaw.getState(), 80, 40); 
        oled.printNumI(digitalRead(irPin1k), 50, 50); 
        oled.printNumI(digitalRead(irPin10k), 80, 50); 
        oled.update(); 
        motorControl.poll(); 
        rightClaw.poll(); 
        leftClaw.poll(); 
    }
}

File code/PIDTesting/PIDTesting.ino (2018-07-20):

#include <phys253.h>
#include <LiquidCrystal.h>

//******* Pins *******//
const int leftMotor = 0;
const int rightMotor = 1;
const int leftQRDPin = 1;
const int rightQRDPin = 0;

const int Kp_pin = 4;
const int Kd_pin = 5;
//const int Ki_pin = 0;
const int K_pin = 6;
const int threshold_pin = 7;

//******* Constants *******//
//Working values:
//Kp = 1, Kd = 4, K = 55
const int defaultMotorSpeed = 160;
int threshold = 1;

int K = 0;
int Kp = 0;
int Ki = 0;
int Kd = 0;
float p;
float i;
float d;

int iMax;
int deadBand;
int error = 0;
int lastError = 0;
int gain;
int count = 0;

bool leftQRDState;
bool rightQRDState;

volatile bool state = false;
int leftMotorSpeed = 0;
int rightMotorSpeed = 0;

void setup() {
  // put your setup code here, to run once:
  #include <phys253setup.txt>
  Serial.begin(9600) ;
}

void loop() {
 
  if (startbutton()){
    state = true;
  }
  if (stopbutton()){
    state = false;
  }

  Kp = analogRead(Kp_pin)/10;
  Kd = analogRead(Kd_pin)/10;
  //Ki = analogRead(Ki_pin)/10;
  K = knob(K_pin)/10;
  threshold = knob(threshold_pin);
  
  // put your main code here, to run repeatedly:
  leftQRDState = analogRead(leftQRDPin) > threshold;
  rightQRDState = analogRead(rightQRDPin) > threshold;
  
  // Case 0: Both on
  if (leftQRDState && rightQRDState){
    error = 0;
  }
  // Case 1: Left off, Right on
  else if (rightQRDState){
    error = -1;
  }
  // Case 2: Right on, Left off
  else if (leftQRDState){
    error = 1;
  }
  // Case 3: Both off
  // Case 3.1: Right previously on
  else if (lastError < 0){
    error = -5;
  }
  // Case 3.2: Left previously on
  else if (lastError > 0){
    error = 5;
  }

  p = Kp*error;
  d = Kd*(error-lastError); //
  i = Ki*error + i;
      if (i > iMax) i = iMax;
      if (i < -iMax) i = -iMax;  
  gain = K*(p + i + d);

  if (state) {
    if (gain < 0){
      leftMotorSpeed = defaultMotorSpeed + abs(gain);
      rightMotorSpeed = defaultMotorSpeed - abs(gain);
      motor.speed(leftMotor, leftMotorSpeed);
      motor.speed(rightMotor, rightMotorSpeed);
    }
    else if (gain > 0){
      rightMotorSpeed = defaultMotorSpeed + abs(gain);
      leftMotorSpeed = defaultMotorSpeed - abs(gain);
      motor.speed(rightMotor, rightMotorSpeed);
      motor.speed(leftMotor, leftMotorSpeed);
    }
    else {
      rightMotorSpeed = defaultMotorSpeed;
      leftMotorSpeed = defaultMotorSpeed;
      motor.speed(rightMotor, rightMotorSpeed);
      motor.speed(leftMotor, leftMotorSpeed);  
    }
  }
  else {
    motor.speed(rightMotor, 0);
    motor.speed(leftMotor, 0);
  }

  lastError = error;

  count++;
  if (count > 2000){
    LCD.clear();
    LCD.setCursor(0, 0);
    LCD.print("Kp:");
    LCD.print(Kp);
    LCD.print(" Ki:");
    LCD.print(Ki);
    LCD.print(" Kd:");
    LCD.print(Kd);
    LCD.setCursor(0, 1); 
    LCD.print("G: ");
    LCD.print(K);
    LCD.print(" T: ");
    LCD.print(threshold);
 
    Serial.print("error");
    Serial.println(error);
    Serial.print("Gain");
    Serial.println(gain);
    Serial.print("Left:");
    Serial.println(analogRead(leftQRDPin));
    Serial.print("Right:");
    Serial.println(analogRead(rightQRDPin));
    Serial.print("Left motor speed: ");
    Serial.println(leftMotorSpeed);
    Serial.print("Right motor speed: ");
    Serial.println(rightMotorSpeed);
    
    count = 0;
  }
  //delay(200);
}

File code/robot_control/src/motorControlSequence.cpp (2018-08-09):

#include "includes.h" 

// flags 
bool firstBridge = true; 
bool firstBridgeSequenceDone = false; 
bool throughGate = false; 
bool beforeStormTroopers = true; 
bool afterStormTroopers = true; 
bool detected1k = false; 
bool irGo = false; 
bool clawStartWait = true; 
bool clawBeforeGate = true; 
bool afterThirdEwok = true; 
bool ohBabyADouble = false; 
bool restartNormalPID = false; 
int reducedSpeed;
int nextState = 0; 
unsigned long nextDelay = 0; 

#define CLAW_POLL 0
#define CLAW_UP 10
#define CLAW_DOWN 11
#define CLAW_PHOENIX 12
#define CLAW_IN 13
#define CLAW_JITTER 14

MotorControl::MotorControl(Motor &leftMotor, Motor &rightMotor, Bridge &bridge, IRReader &ir, 
    Basket &basket, TapeFollow &pidControl, ClawSequence &leftClaw, ClawSequence &rightClaw, int qrdThreshold, int gain, int p, int i, int d) 
: leftMotor(leftMotor), rightMotor(rightMotor), bridge(bridge), ir(ir), basket(basket), pidControl(pidControl), leftClaw(leftClaw), rightClaw(rightClaw)
{ 
    this->qrdThreshold = qrdThreshold;  
    this->gain = gain; 
    this->pVal = p; 
    this->iVal = i; 
    this->dVal = d; 

    // Initialize bridge angle 
    // bridge.firstBridgeLowerAngle = 40;
    // bridge.firstBridgeUpperAngle = 130; 

    reducedSpeed = 130; // no need for this for now
}

void MotorControl::begin() { 
    leftMotor.begin(); 
    rightMotor.begin(); 
    bridge.begin(); 
    basket.begin(); 
    ir.begin(); 
    pidControl.begin(); 
    leftClaw.begin(); 
    rightClaw.begin(); 
}

void MotorControl::reset() { 
    firstBridge = true; 
    firstBridgeSequenceDone = false; 
    throughGate = false; 
    beforeStormTroopers = true; 
    detected1k = false; 
    irGo = false; 
    clawStartWait = true; 
    ohBabyADouble = false; 
    afterStormTroopers = true; 
    clawBeforeGate = true;
    afterThirdEwok = true; 
}

void MotorControl::specialStateChecker() {
    // Special state delay is used to prevent repeating a state (i.e restarting first bridge sequence multiple times as
    // it pulls away from the edge)
    
    if (millis() < specialStateDelay) { 
        return; 
    }

    // Switch to first bridge sequence
    if (ewokCounter == 1 && firstBridge) { 
        state = 7;
        delay = millis() + 50;  
        firstBridge = false; 
    }

    // IR special sequences  
    if (firstBridgeSequenceDone == true) { 
        if (detected1k == false) { 
            // Switch to wait state
            state = 100;  
            if (ir.read1k()) {detected1k = true;}
            leftClaw.stateOverride(CLAW_UP);
        }
        else if ((ir.read10k() && !ir.read1k()) && detected1k == true) { 
            if (irGo == false) { 
                state = 2; 
                irGo = true; 
            }
        }
    }

    if (ewokCounter > prevEwokCounter) { 
        nextState = state; 
        // delay = millis() + 200; 
        nextDelay = 0; 
        // state = 101; 
        prevEwokCounter = ewokCounter; 
    }
    if (ewokCounter == 2 && clawBeforeGate) { 
        specialStateDelay = millis() + 1350; 
        leftClaw.stateOverride(CLAW_UP); 
        clawBeforeGate = false;  
    }
    if (ewokCounter == 2 && !throughGate) { 
        // Second ewok has been picked and dropped, put hands up 
        // Note the special delay from above is to prevent the claw from closing
        // before it has dropped the ewok

        // Freeze, both hands up! oh god please don't shoot please im too yung
        if (millis() > specialStateDelay) { 
            restartNormalPID = true; 
            rightClaw.stateOverride(CLAW_UP); 
            reducedSpeed = 190; // Revert back to default speed
            throughGate = true;
            specialStateDelay = millis() + leftClawDownDelay; // delay to get from gate to after storm troopers before bringing left claw down 
        }
    }
    if (millis() > specialStateDelay && ewokCounter == 2 && beforeStormTroopers && throughGate) { 
        // We've passed Stormy Daniels, bring left claw down (but wait before polling to prevent it triggering itself)
        leftClaw.stateOverride(CLAW_DOWN); 
        rightClaw.stateOverride(CLAW_UP); 

        beforeStormTroopers = false; 
        specialStateDelay = millis() + 500; 
    }
    if (millis() > specialStateDelay && !beforeStormTroopers && clawStartWait) { 
        // Start left claw polling
        leftClaw.stateOverride(CLAW_JITTER); 
        clawStartWait = false; 
    }

    if (ewokCounter == 3 && afterStormTroopers) { 
        // Sequence to switch to after third ewok
        state = 39; 
        afterStormTroopers = false; 
        delay = millis() + 3000; 
        specialStateDelay = millis() + 3000; 
    }
    if (ewokCounter == 3 && afterThirdEwok && !afterStormTroopers) { 
        // Bring left claw back up after ewok has been picked and dropped
        if (millis() > specialStateDelay) { 
            leftClaw.stateOverride(CLAW_UP); 
            afterThirdEwok = false; 
        }
    }
}
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

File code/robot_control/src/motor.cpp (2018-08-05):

#include "includes.h"  

Motor::Motor(){}; // Default constructor 

Motor::Motor(int motorPin1, int motorPin2) { 
    // Important: ensure that the pin used is a PWM capable port. 
    // Refer to https://camo.githubusercontent.com/57179305662a573319afec320712289880a7f134/687474703a2f2f77696b692e73746d33326475696e6f2e636f6d2f696d616765732f612f61652f426c7565706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

    this->motorPin1 = motorPin1;
    this->motorPin2 = motorPin2; 
}

void Motor::begin() { 
    analogWrite(0, motorPin1); 
    pinMode(motorPin1, OUTPUT);
    
    delay(50); 

    analogWrite(0, motorPin2); 
    pinMode(motorPin2, OUTPUT); 
}

void Motor::forward(int speed) {
    // Accepts positive integers between 0-255. 
    // Runs the motors forward (check polarity of wiring).
    analogWrite(motorPin1, speed); 
    analogWrite(motorPin2, 0); 
}

void Motor::reverse(int speed) { 
    // Accepts positive integers only between 0-255. 
    // Runs the motors in reverse (check polarity of wiring).
    analogWrite(motorPin1, 0); 
    analogWrite(motorPin2, speed); 
}

void Motor::write(int speed) { 
    if (speed > 255) {speed = 255;}
    else if (speed < -255) {speed = -255;}
    
    if (speed >= 0) {forward(speed);}
    else if (speed < 0) {reverse(abs(speed));}
}

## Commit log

2018-05-22 embedded cad attempt 1
    [AlexEzzat_54_MaleSide.STL]
2018-05-22 embedding a cad model
2018-05-28 reorganized site docs
    [AlexEzzat_54_MaleSide.STL]
2018-05-28 added site folder
    [AlexEzzat_54_MaleSide.STL]
2018-05-28 site in docs folder
    [AlexEzzat_54_MaleSide.STL]
2018-05-28 fixing folder strucure
    [AlexEzzat_54_MaleSide.STL]
2018-05-28 folder for cad models and general images
2018-05-29 first PID test code
2018-05-30 enph257 lab code, arduino+reading from serial
2018-06-04 ENPH 257 direct logging to SD card + automated power modulation
2018-06-06 first model
    [FlatBot - 3in Wheel-1.STL, FlatBot - 3in Wheel-2.STL, FlatBot - 3in Wheel-3.STL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]
2018-06-06 assembly in one STL now...
    [FlatBot.STL]
2018-06-06 working on PID control
2018-06-08 Filtered data for trial8
    [Trial8_2018-04-06-17_00_cycle700s_duration2h_filtered.csv]
2018-06-13 third good dataset, horizontal, different power
2018-06-15 Updated simulation code and excel file for variable adjustments
    [Test Variables.xlsx]
2018-06-18 Added Electrical Schematics
    [Robot Electrical Schematic June 17th.dsn]
2018-06-21 Elec diagram june 19th
    [Robot Electrical Schematic June 19th.dsn]
2018-06-23 Added STM32 LT 1161 H Bridge
    [STM 1161 H-Bridge.dsn]
2018-07-04 Updated with STM32 info
2018-07-06 Electrical Content Updated. Voltage Regulator, Voltage Inverter, etc.
    [Cascading Voltage Inverter.dsn, STM 1161 H-Bridge.dsn, Voltage Inverter.dsn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]
2018-07-08 robot control code. Added bridge and claw sequences, needs modification. Read README for TODOs etc.
2018-07-11 Added local servo lib, fixed pins for servos, also random enph257 data that hasn't been committed
    [main.cpp]
2018-07-11 motor object
2018-07-11 Motor control code framework, skeleton IR class, started adding state logic framework for changing between unique sequences i.e bridges/IR
2018-07-11 Added motor control object to main
2018-07-11 Fixed writing to motor, requires two pins. Added gain constant for PID
    [main.cpp, motor.cpp]
2018-07-13 motor control updates, pin changes possibly
2018-07-13 Included functions to independently control left and right motor speed, because we have a gimpped motor...
2018-07-16 Added encoder files, removed include motor.h from motor files, edits in motor controll sequence and main for direction testing on Friday July 13
2018-07-16 Encoder Updates
2018-07-16 Added PID variables to motorControl
2018-07-16 Finished Encoder Class, added wheel diameter to includes
2018-07-16 Fixed encoder ifs
2018-07-17 Claw test
2018-07-17 New main, changes to clawSequence
2018-07-18 Motor initialization, should guard against burning anymore STMs
    [main.cpp]
2018-07-18 Motor initialization files
2018-07-18 Updated motorinit
2018-07-18 Updated claw sequence delay variables to be more descriptive
2018-07-18 Tape following files, and addition into motor control
2018-07-18 PID Menu systeM
2018-07-18 Fixed missing equals operator
    [main.cpp]
2018-07-19 removed claw serial print
2018-07-20 PID code updates
2018-07-20 Testing code used with V2
    [Acrylic DXF.dxf, BasketRodHolderx3.DXF, BasketV3BackPanel.DXF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]
2018-07-20 Differentiated between left, right and default motor speeds.
2018-07-20 Updated PID control
2018-07-20 Added claw servo angle parameter
2018-07-21 Updated claw with additional angle parameters
2018-07-24 Added additional angle parameters, custom angle for when claw opens inside chassis
2018-07-24 Fixed duplicate of leftmotor reverse, updated pinouts on main
    [main.cpp, motorControlSequence.cpp]
2018-07-24 unified forward/reverse motor functions
    [motor.cpp, motorControlSequence.cpp]
2018-07-26 latest pid/motor stuff
2018-07-26 Pick up Ewok and return motor control sequence
2018-07-27 refactored motorControl to couple bridge and claw mechanisms
2018-07-28 Added state to lower claw
2018-07-31 Sequence updates, added encoder motion into motor control
2018-08-01 Latest update, currently testing bridge deployment
2018-08-02 IR logic, claw overrides
2018-08-06 Added custom phoenix angle function to claw for deploying basket
2018-08-06 Added rotary jolts to guard against inertial slides, also fixed issue of LClaw repeating sequence after picking 3rd ewok
    [main.cpp, motorControlSequence.cpp]
2018-08-13 rearranged files. Open and full are the ones we should use for the website
    [Acrylic DXF.dxf, BasketRodHolderx3.DXF, BasketV3BackPanel.DXF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]
2018-08-13 Added CAD screenshots
2018-08-13 Added chassis view, renamed folder
2018-08-16 Added IR circuits
    [IRBeacon-10k.dsn, IRBeacon-1k.dsn]
2018-08-16 IR circuit images
